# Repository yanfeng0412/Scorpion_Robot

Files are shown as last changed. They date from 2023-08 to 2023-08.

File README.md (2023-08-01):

# Scorpion_Robot
 The hexapod scorpion robot is designed with MG995 servos to control the joint angles, providing 3 degrees of freedom for each joint. The robot has two hands and a tail joint designed using biomimetic principles. It uses both MG995 and SG90 servos for driving. The PWM signals for the servos are expanded to 32 channels using PCA9685.
 
# The main tasks of the project are as follows:
  1. 3D Modeling of the robot (Solidworks2022)
  2. PCB Circuit Design(Altium Designer)
  3. Establishment of the mathematical model simulation system for the robot(ROS-Gazebo, Pybullet and Matlab)
  4. Forward and inverse kinematic calculation for the robot.
  5. Robot GUI/HMI Design (HTML and Android Studio)
  6. Robot's Gait Design (Arduino IDE)

This project primarily controls 25 servos, thus requiring two PCA9685 modules to expand the PWM signals for the servos. The communication between PCA9685 and the ESP main controller is established using I2C protocol. Additionally, the addresses of the two PCA9685 modules need to be set as 0x40 and 0x41 to distinguish the communication targets.

# Documentation
## 1. 3D Model Scorpion Robot MG995

  The file is modeled based on the MG995 servo motor. The hand joints of the robot are driven by bevel gears to achieve freedom along the z-axis. Meanwhile, the tail joint of the robot is designed using a biomimetic mechanical finger structure as a reference.
## 2. 3D Model Scorpion Robot SG90

   The file is primarily designed using the SG90 servo motor for the robot. However, due to the limited driving torque of the SG90 and issues with the quality of plastic servos, this design version faces challenges in achieving the set objectives. As a result, it is only included here for reference purposes.
## 3. Control Code
   Inside, it is mainly divided into the following sections:
   ### 3.1 Gait Control
   Programming the robot's gait using forward kinematics algorithms.The two files represent the user interfaces (UI) for the robot's control system. One is developed using Android Studio, and the other is an HTML version.
       3.1.1
       Android Studio Version (Android Studio)
       3.1.2
       HTML Version (Arduino IDE + HTML)
   ### 3.2 Inverse Kinematic    
   The file mainly adjusts the robot's posture using inverse kinematics. Based on this, the inverse kinematics can be integrated with sensors like MPU6050 to achieve closed-loop control of the robot's motion/pose.
## 4. ESPCAM
   By programming ESPCAM, this file is used for the vision system of the robot.
## 5. PCB_Robot
   The file is the PCB circuit design of the robot, created using Altium Designer 23 to layout the components on the module.

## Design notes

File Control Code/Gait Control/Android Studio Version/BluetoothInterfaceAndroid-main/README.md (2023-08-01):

# BluetoothInterfaceAndroid
An app that is built using Android Studio and Java. Can be used to interface your android smartphone to a bluetooth device like HC-05 and transmit and receive data. 
It has 5 built in buttons that are mapped to control the direction of the motor(vehiche) in our case. But the buttons can be mapped to any values of choice by just long 
pressing and setting the value of them.
The UI of the app looks like below.

My project-1

Feel free to use the code and modify the contents according to your requirement. Also if anyone wants to modify or optimize the code can send their requests.

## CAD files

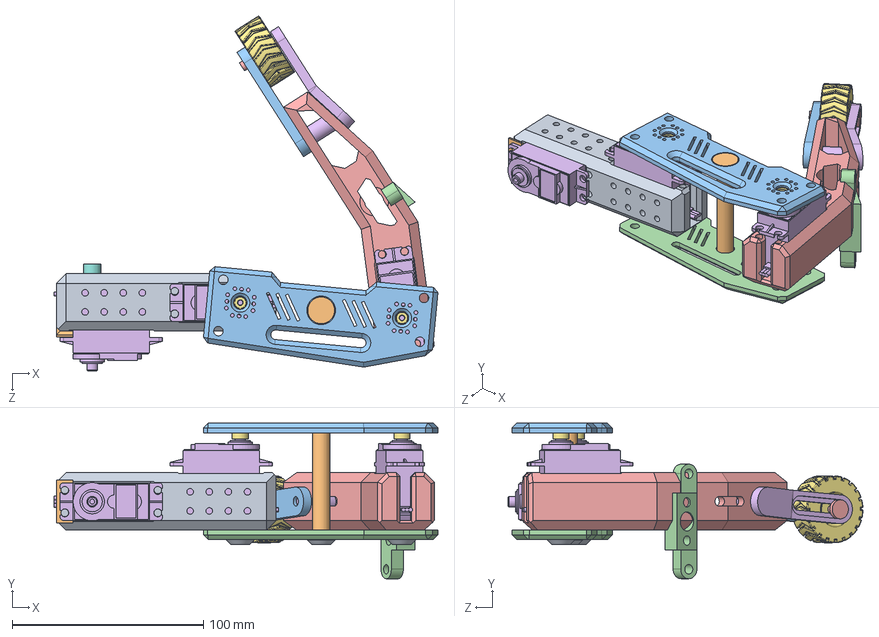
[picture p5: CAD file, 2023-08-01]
3D Model Scorpion Robot MG995/LEG3/LASM.SLDASM
201.0 x 81.4 x 185.8 mm
L0
L1
L2
L3
L4
MG995Servo x 3
wheel_MG995 x 2
L5 x 3
L6 x 3
L7
WheelLink2
L8
WheelLink4
WheelLink
wheel

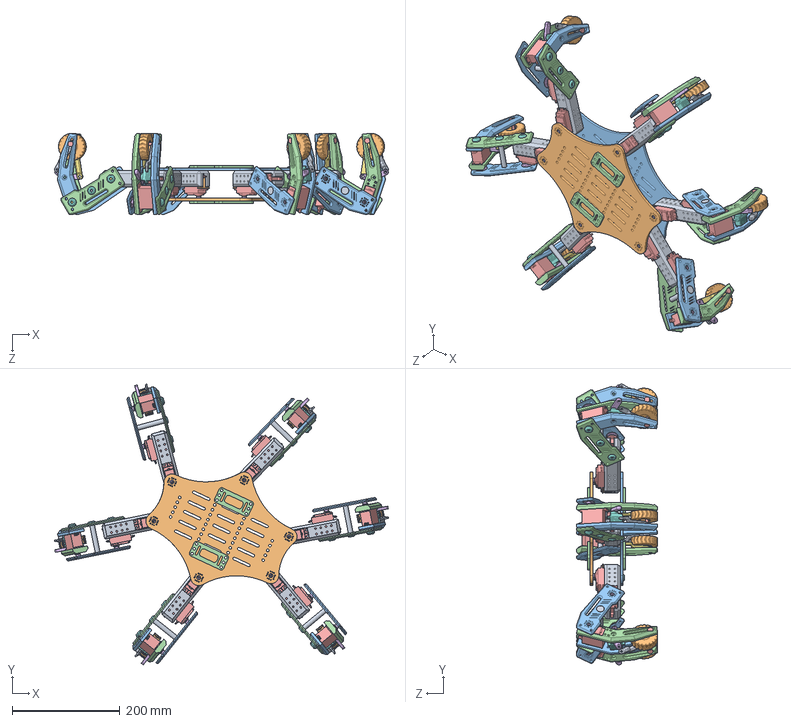
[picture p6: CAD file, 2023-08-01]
3D Model Scorpion Robot MG995/OVR2.SLDASM
621.1 x 522.3 x 151.2 mm
L0 x 6
L1 x 6
L2 x 6
L3 x 6
MG995Servo x 18
wheel_MG995 x 18
L5 x 19
L6 x 19
L7 x 6
wheel x 6
L4.1 x 6
L4.2 x 6
WheelLink4 x 12
WL2 x 6
WL1 x 6
SG90 - Micro Servo 9g - Tower Pro.1 x 6
WL3 x 6
base4.1
base3.1
cnl x 4

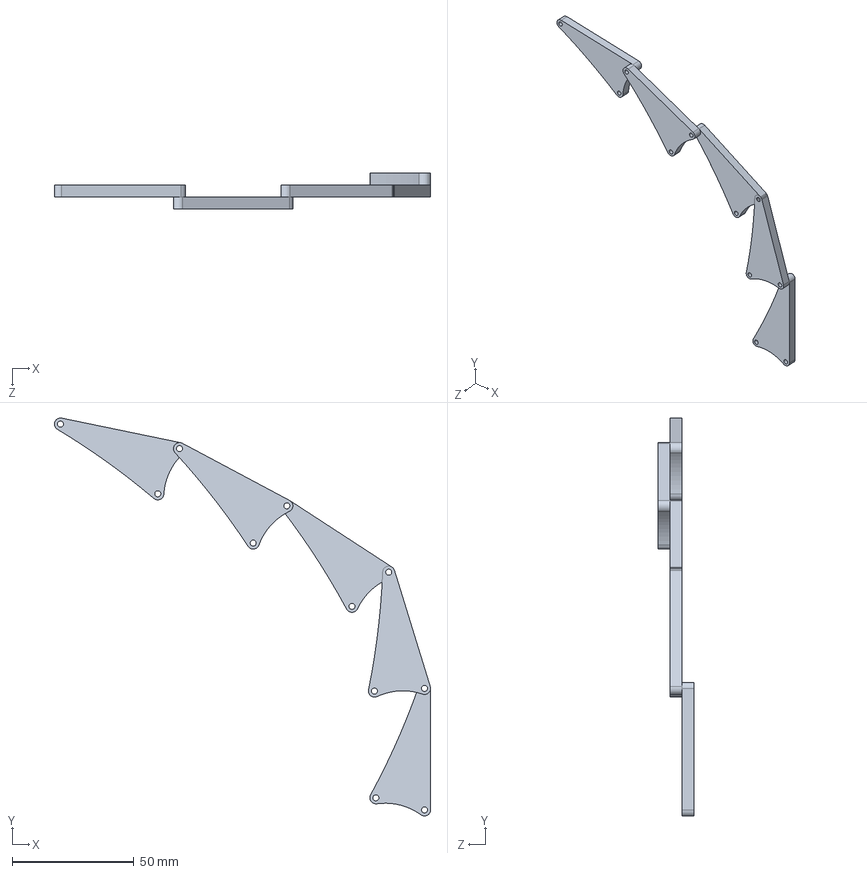
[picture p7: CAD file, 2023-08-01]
3D Model Scorpion Robot MG995/Tail/TailAssem.SLDASM
154.7 x 163.7 x 15.0 mm
T4 x 5

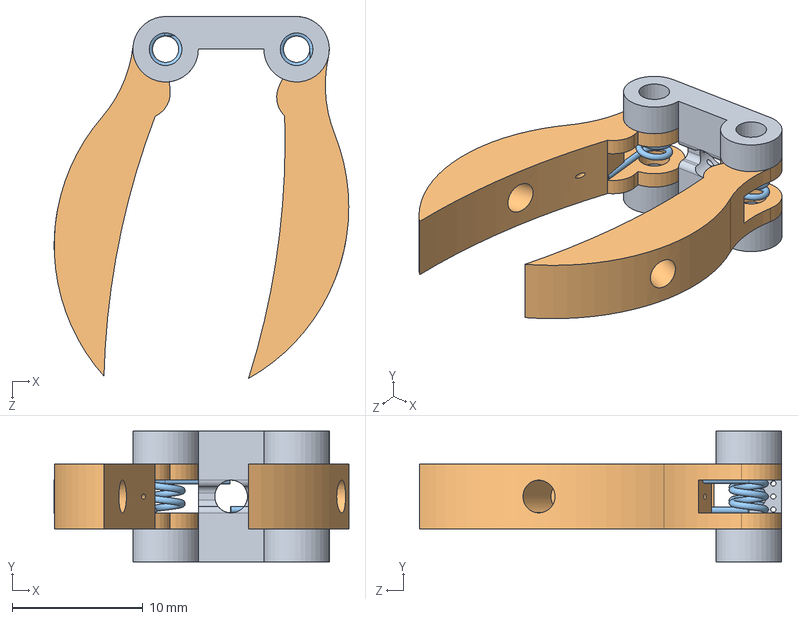
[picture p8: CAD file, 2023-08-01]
3D Model Scorpion Robot SG90/Hand/Claw2.SLDASM
22.5 x 10.0 x 27.6 mm
Claw1
Claw2 x 2
clawspring x 2

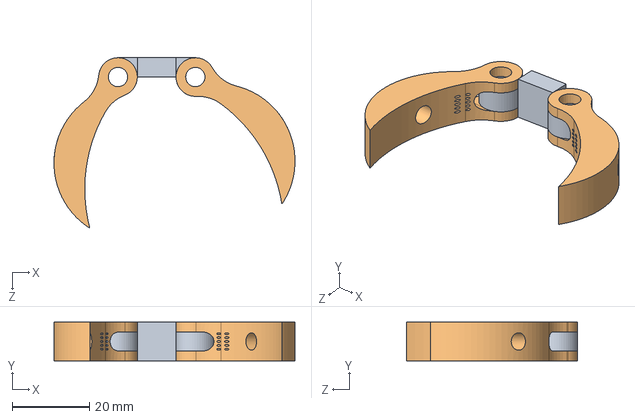
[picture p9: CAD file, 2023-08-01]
3D Model Scorpion Robot SG90/Hand2/ClawAse.SLDASM
62.3 x 10.0 x 44.1 mm
Claw1
Claw2 x 2

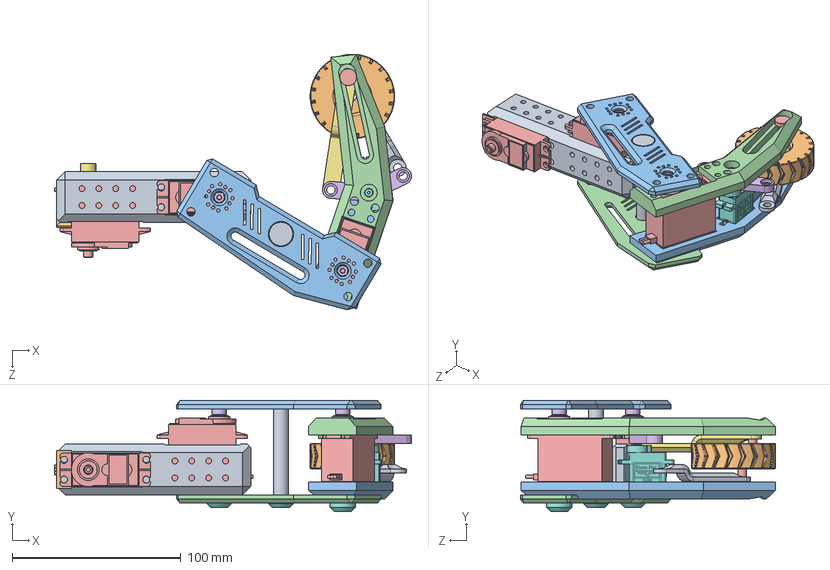
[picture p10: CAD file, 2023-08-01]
3D Model Scorpion Robot MG995/LEG2/LASM.SLDASM
211.3 x 65.9 x 151.2 mm
L0
L1
L2
L3
MG995Servo x 3
wheel_MG995 x 2
L5 x 3
L6 x 3
L7
wheel
L4.1
L4.2
WheelLink4 x 2
WL2
WL1
SG90 - Micro Servo 9g - Tower Pro.1
WL3

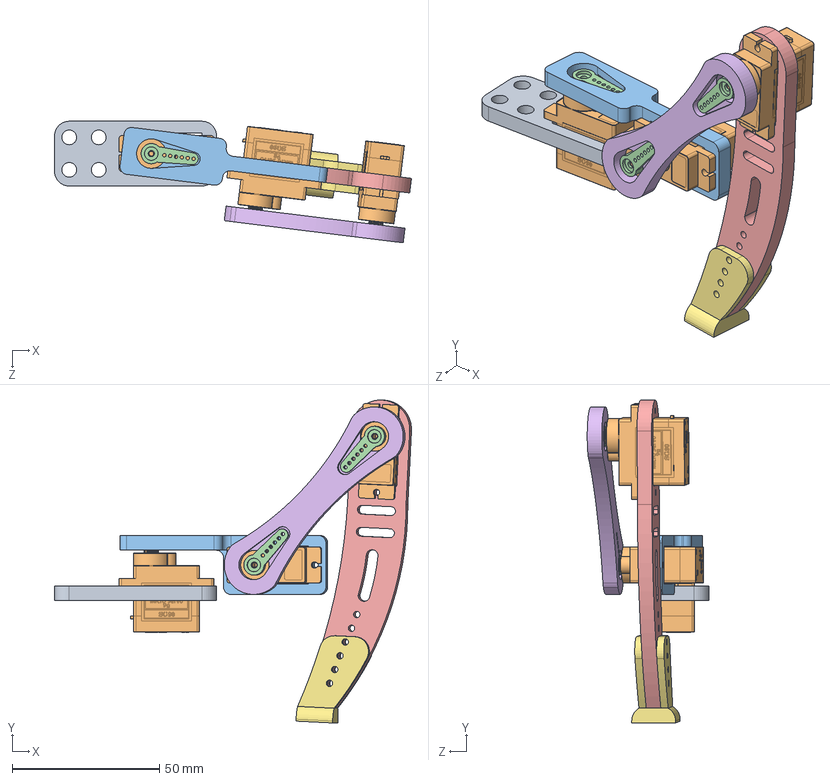
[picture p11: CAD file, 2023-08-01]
3D Model Scorpion Robot SG90/LegAs.SLDASM
121.1 x 109.6 x 41.3 mm
L1.0
SG90 - Micro Servo 9g - Tower Pro.1 x 3
L1
SG90 - Micro Servo 9g - Tower Pro.2 x 3
L3
L2
L4

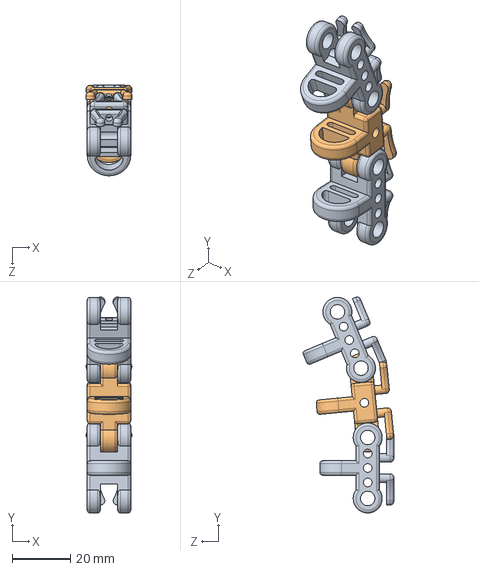
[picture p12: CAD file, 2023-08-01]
3D Model Scorpion Robot SG90/Tail/TAS/Assem1.SLDASM
15.8 x 74.4 x 31.2 mm
Tx1 x 2
Tx2

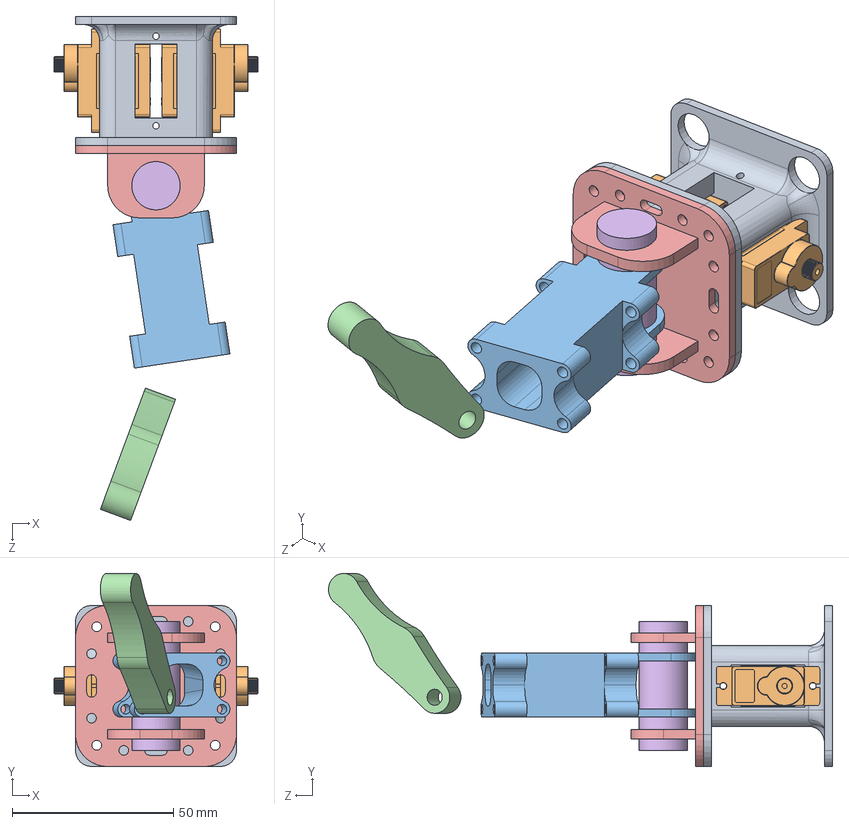
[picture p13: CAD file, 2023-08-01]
3D Model Scorpion Robot SG90/Tail/TAS2/As.SLDASM
63.3 x 59.9 x 156.4 mm
B1
SG90 - Micro Servo 9g - Tower Pro.1 x 2
T1
T2
T3
Strud

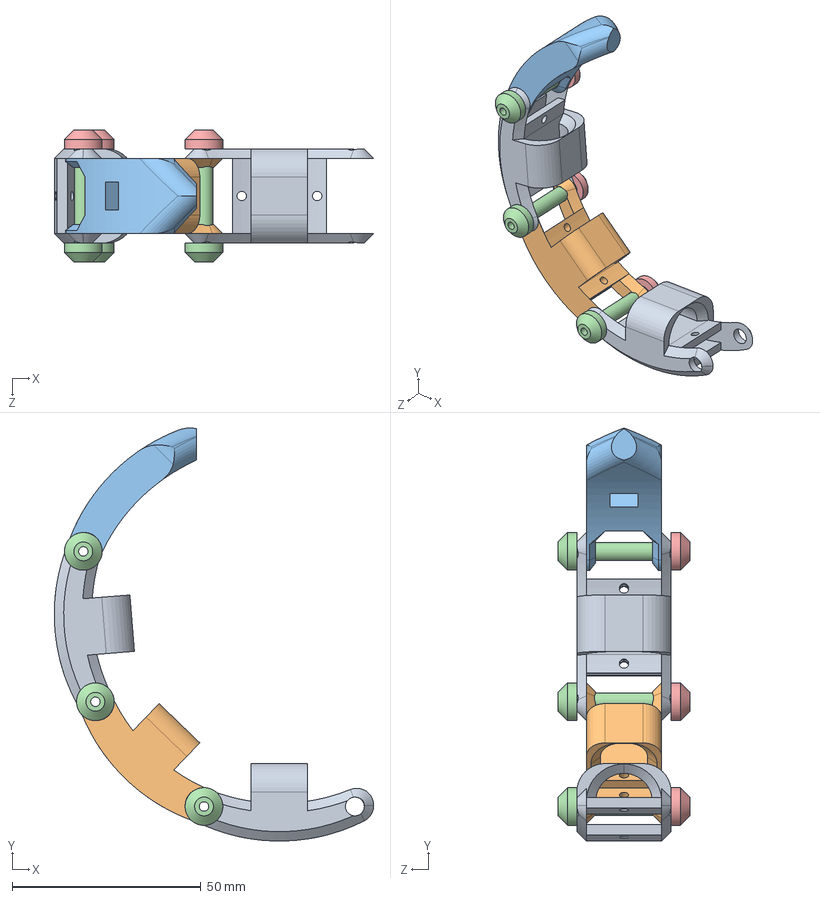
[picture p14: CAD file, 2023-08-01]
3D Model Scorpion Robot SG90/Tail/TailTensor/ase.SLDASM
84.7 x 109.5 x 35.0 mm
t2 x 2
t3
t4
nut x 3
bolt x 3

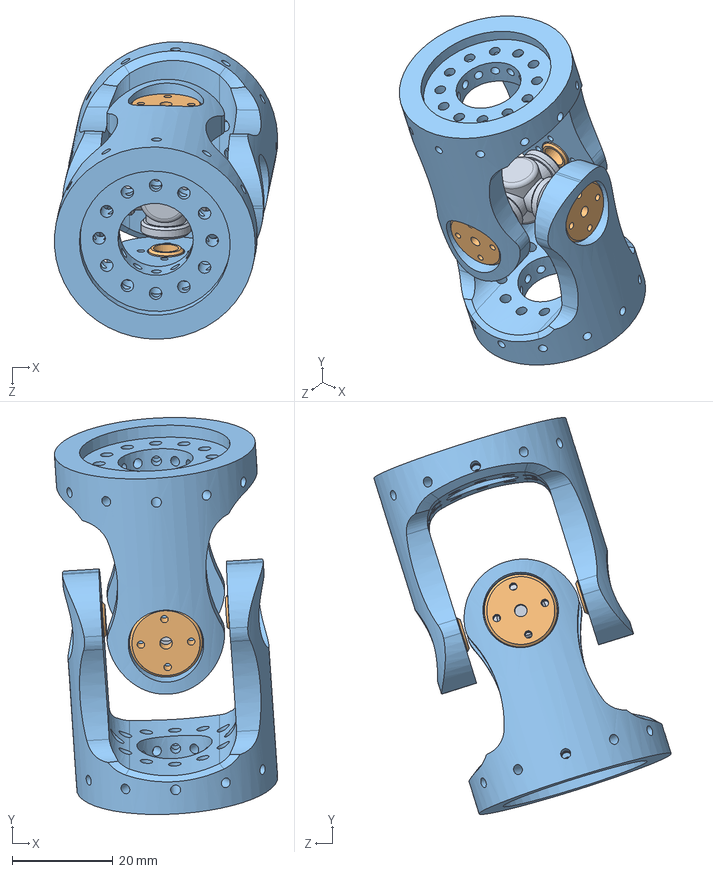
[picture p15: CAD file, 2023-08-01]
3D Model Scorpion Robot SG90/Tail/UVSTail2/Tail 2.SLDASM
44.4 x 78.9 x 59.1 mm
uvs2
uvs4 x 4
uvs1.2 x 2

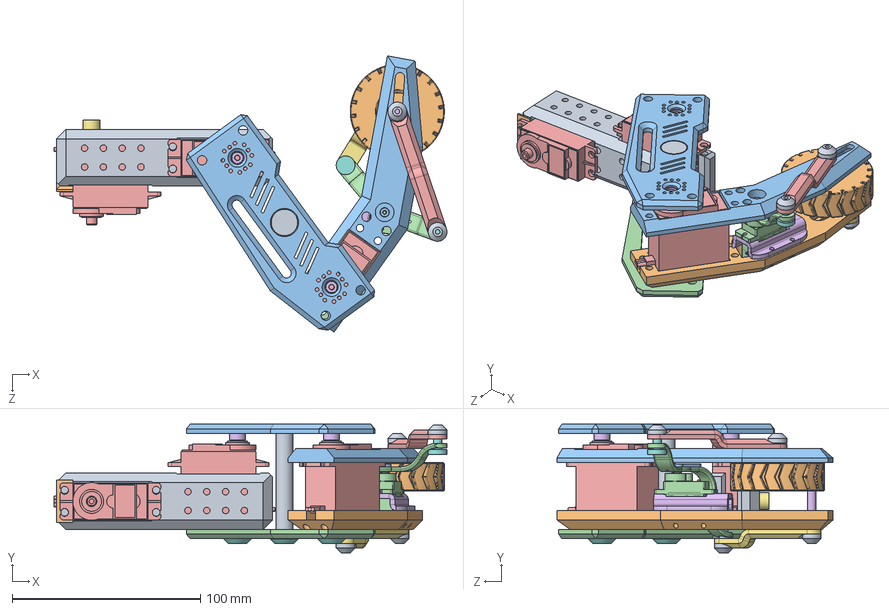
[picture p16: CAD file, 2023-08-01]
3D Model Scorpion Robot MG995/LEG4/LGASM2.SLDASM
209.0 x 68.4 x 146.9 mm
LG0
LG1
LG2
LG3
MG995Servo x 3
wheel_MG995 x 2
LG5 x 3
LG6 x 3
LG7
LG4.1
LG4.2
SG90 - Micro Servo 9g - Tower Pro.1
WL1
WL4 x 2
WL3
WL5 x 2
WLNUT1 x 4
wheel
SG90 - Micro Servo 9g - Tower Pro.2
WL2AS1
WL6
WL7

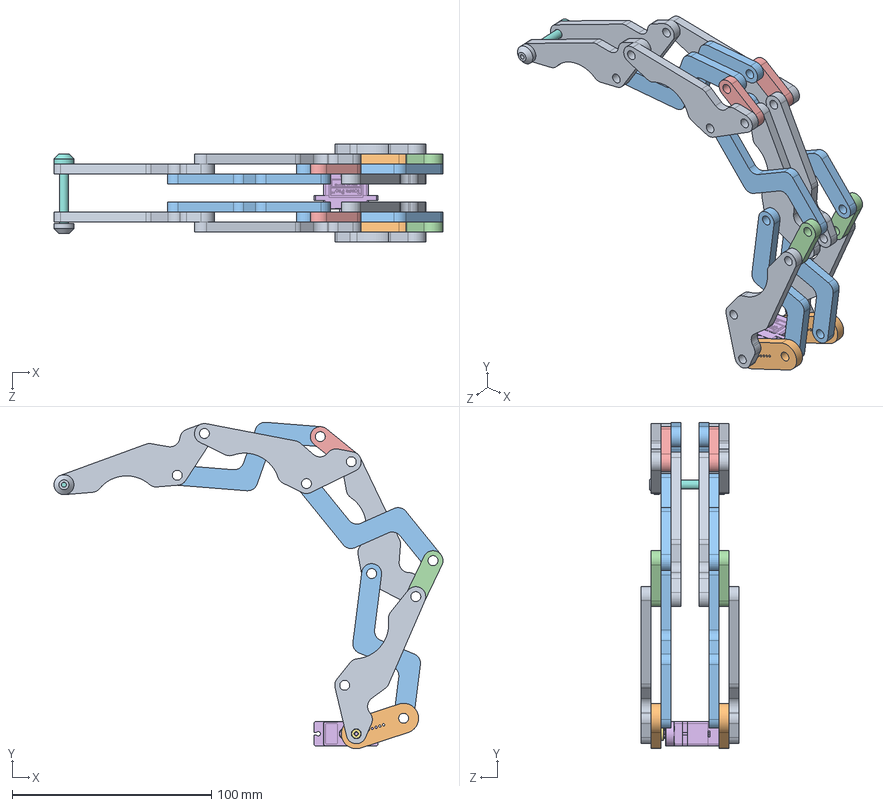
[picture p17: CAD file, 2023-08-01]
3D Model Scorpion Robot MG995/Tail3/Tail3Asm2.SLDASM
195.1 x 163.7 x 49.2 mm
T1 x 8
T2 x 2
T3 x 6
T4 x 2
T5 x 2
SG90 - Micro Servo 9g - Tower Pro.1
SG90 - Micro Servo 9g - Tower Pro.2
TL3
TL2

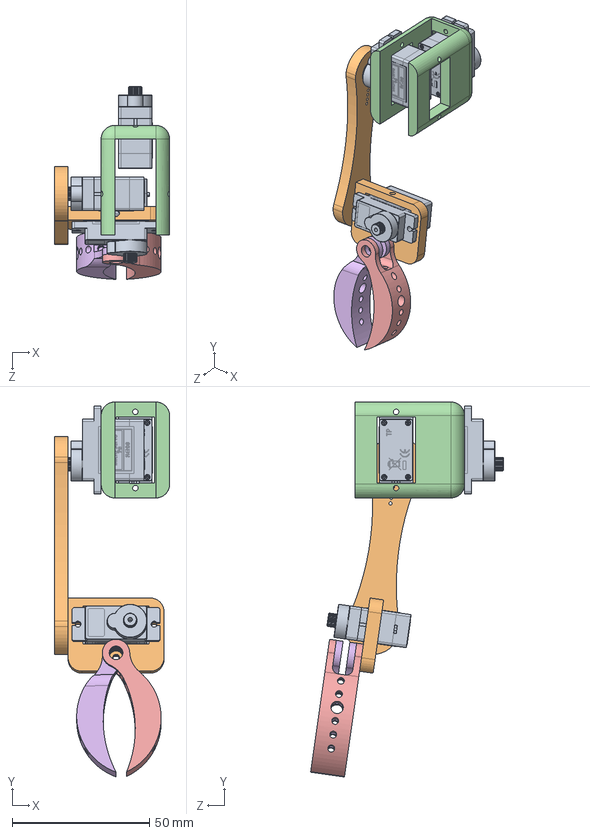
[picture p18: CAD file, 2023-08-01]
3D Model Scorpion Robot SG90/Hand/HandAsem.SLDASM
42.0 x 136.8 x 70.3 mm
SG90 - Micro Servo 9g - Tower Pro.1 x 3
hand6
SG90 - Micro Servo 9g - Tower Pro.2
hand5.1
Claw4
Claw4.1

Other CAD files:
3D Model Scorpion Robot SG90/Hand2/ClawAse2.SLDASM
3D Model Scorpion Robot MG995/Tail3/Tail3Asm.SLDASM
3D Model Scorpion Robot MG995/OVR3.SLDASM
3D Model Scorpion Robot MG995/Tail2/Tail2Asm.SLDASM
3D Model Scorpion Robot MG995/Hand1/Claw1.SLDPRT
3D Model Scorpion Robot MG995/Hand1/Claw2.SLDPRT
3D Model Scorpion Robot MG995/Hand1/Claw3.SLDPRT
3D Model Scorpion Robot MG995/Hand1/ClawAsm.SLDASM
3D Model Scorpion Robot MG995/Hand1/ClawLink1.SLDPRT
3D Model Scorpion Robot MG995/Hand1/ClawLink2.SLDPRT
3D Model Scorpion Robot MG995/Hand1/HL0.1.1.SLDPRT
3D Model Scorpion Robot MG995/Hand1/HL0.1.2.SLDPRT
3D Model Scorpion Robot MG995/Hand1/HL0.2.SLDPRT
3D Model Scorpion Robot MG995/Hand1/HL0.SLDPRT
3D Model Scorpion Robot MG995/Hand1/HL1.SLDPRT
3D Model Scorpion Robot MG995/Hand1/HL2.SLDPRT
3D Model Scorpion Robot MG995/Hand1/HandAsm.SLDASM
3D Model Scorpion Robot MG995/Hand1/HandBase1.SLDPRT
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

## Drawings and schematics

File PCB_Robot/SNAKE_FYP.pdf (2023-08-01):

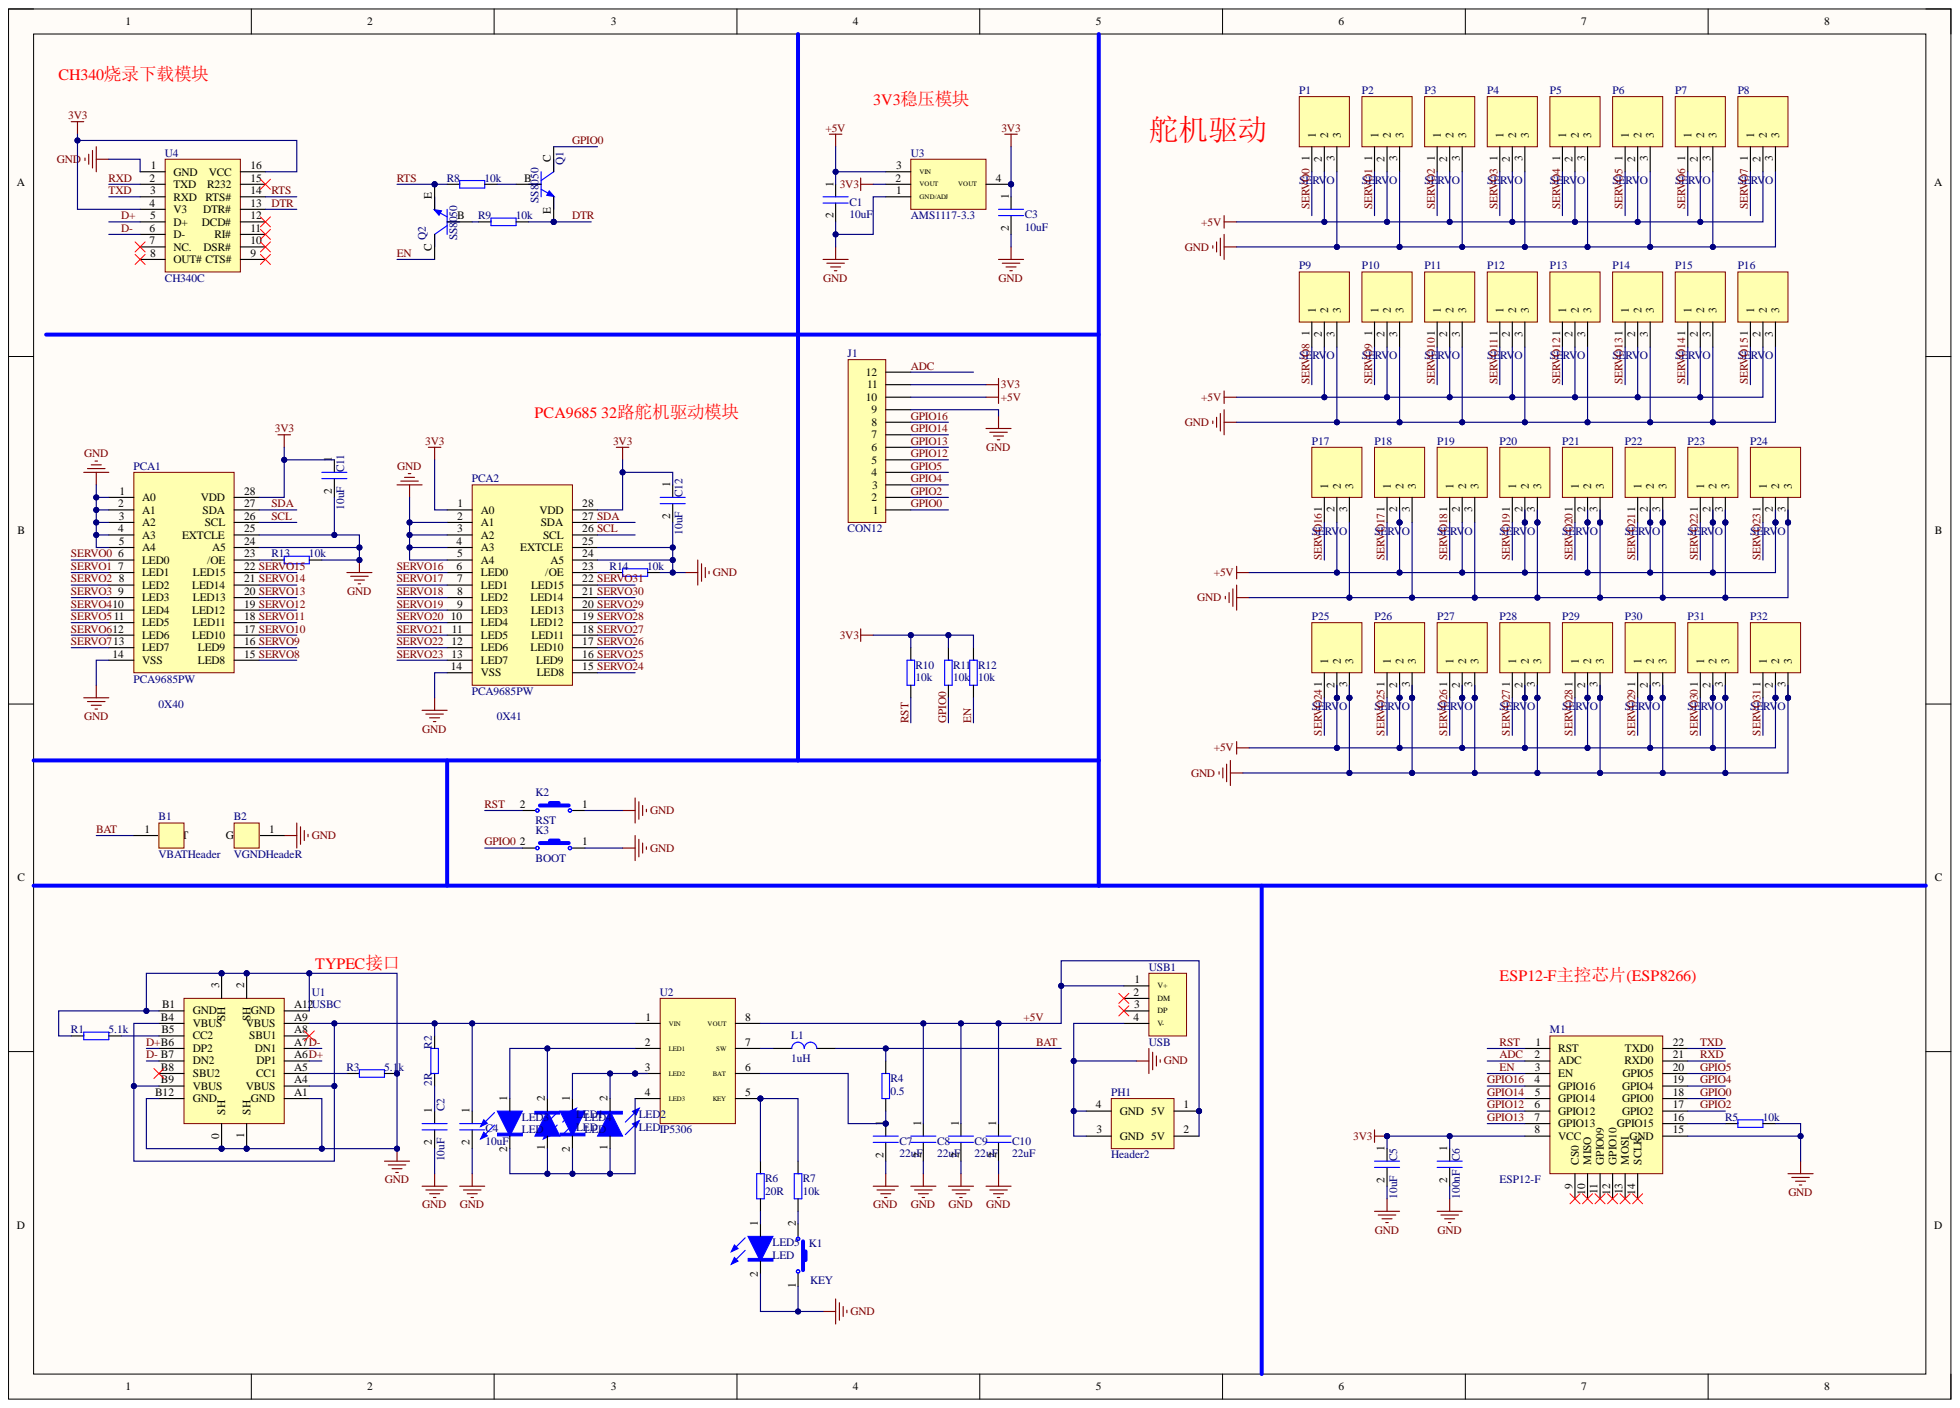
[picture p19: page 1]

SH 1 GND A1 VBUS A4 CC1 A5 DP1 A6 DN1 A7 SBU1 A8 VBUS A9 GND A12

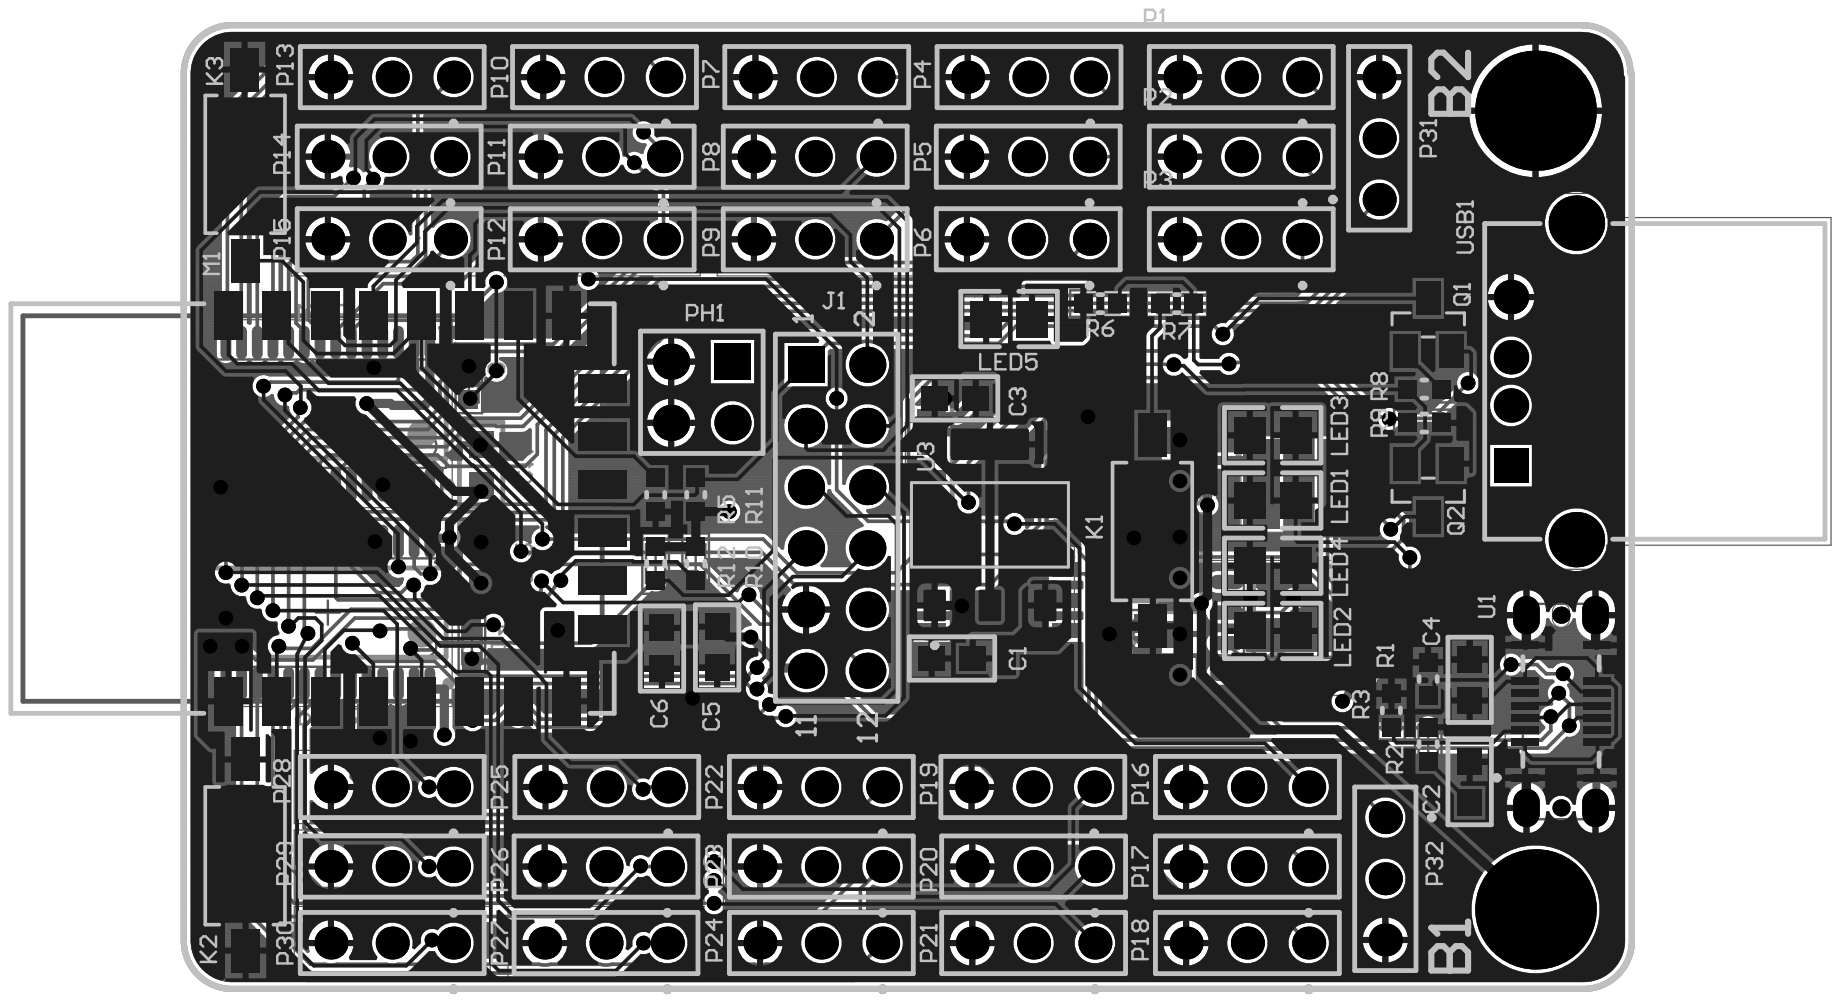
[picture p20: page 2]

Comment | Description | Designator | Footprint | LibRef | Quantity
VBATHeader | | B1 | 18650VBAT | VBATHeader | 1
VGNDHeadeR | | B2 | 18650GND | VGNDHeadeR | 1
10uF | 电容 | C1, C2, C3, C4, C5, C11, C12 | Cap-0603 | CAP | 7
100nF | 电容 | C6 | Cap-0603 | CAP | 1
22uF | 电容 | C7, C8, C9, C10 | Cap-0603 | CAP | 4
CON12 | Connector | J1 | HDR2X6 | CON12 | 1
KEY | 按键 | K1 | TSW SMD-3*6*2.5(Button) | RST | 1
RST | 按键 | K2 | TSW SMD-3*6*2.5(Button) | RST | 1
BOOT | 按键 | K3 | TSW SMD-3*6*2.5(Button) | RST | 1
1uH | 电感 | L1 | CDRH3D16_4.2*1.8 | INDUCTOR | 1
LED | | LED1, LED2, LED3, LED4, LED5 | LED-0805 | LED | 5
ESP12-F | | M1 | ESP-12F | ESP12-F | 1
SERVO | | P1, P2, P3, P4, P5, P6, P7, P8, P9, P10, P11, P12, P13, P14, P15, P16, P17, P18, P19, P20, P21, P22, P23, P24, P25, P26, P27, P28, P29, P30, P31, P32 | SERVOHEADER | SERVO | 32
PCA9685PW | | PCA1, PCA2 | PCA9685TSOP28 | PCA9685PW | 2
Header2 | | PH1 | HDR2X2 | Header2 | 1
SS8050 | | Q1, Q2 | SOT-23_BEC(SS8050) | SS8050 | 2
5.1k | 电阻 | R1, R3 | 0603_RES | RES | 2
2R | 电阻 | R2 | 0603_RES | RES | 1
0.5 | 电阻 | R4 | 0603_RES | RES | 1
10k | 电阻 | R5, R7, R8, R9, R10, R11, R12, R13, R14 | 0603_RES | RES | 9
20R | 电阻 | R6 | 0603_RES | RES | 1
USBC | | U1 | TYPEC | USBC | 1
IP5306 | 升压、降压和锂电池 充电管理芯片 | U2 | ESOP_IP5306 | IP5306 | 1
AMS1117-3.3 | | U3 | SOT229P700X180-4N(AMS1117-3.3) | AMS1117-3.3 | 1
CH340C | | U4 | SO016_CH340 | CH340 | 1
USB | | USB1 | TypeA | USB | 1

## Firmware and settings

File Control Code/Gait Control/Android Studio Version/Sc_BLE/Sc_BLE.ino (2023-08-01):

 #include <Wire.h>
#include <Adafruit_PWMServoDriver.h>
Adafruit_PWMServoDriver pwm = Adafruit_PWMServoDriver(0x40);
Adafruit_PWMServoDriver pwm1 = Adafruit_PWMServoDriver(0x41);
#define SERVOMIN 102
#define SERVOMAX 500
#include <ESP32Servo.h>
#include "BluetoothSerial.h"

BluetoothSerial serialBT;
char cmd;



double a0; double a1; double a2; double a3;
int leg1[] = {0,1,2};int leg2[] = {3,4,5}; int leg3[] = {6,7,8};
int leg4[] = {9,10,11}; int leg5[] = {12,13,14}; int leg6[] = {15,0,1};


double theta1;
double theta2;
double theta3; 
double theta4;
double theta5;
double theta6;

// 更改tf k
void setup() {
  pwm.begin();
  pwm.setPWMFreq(50);
  pwm.setOscillatorFrequency(27000000);
  pwm1.begin();
  pwm1.setPWMFreq(50);
  pwm1.setOscillatorFrequency(27000000);
  Serial.begin(115200);
  serialBT.begin("ESP32-BT");
  pinMode(2,OUTPUT);
}

void loop(){
  if (serialBT.available()){
    cmd = serialBT.read();
  }
  if(cmd == '1'){
        forward(); 
        digitalWrite(2,HIGH);
     }
  if(cmd == '2'){
        backward(); 
        digitalWrite(2,LOW);
    }
  if(cmd == '3'){
        turnright(); 
        digitalWrite(2,HIGH);
    }
  if(cmd == '4'){
        turnleft(); 
        digitalWrite(2,LOW);
     }  
  if(cmd == '5'){
        stand(); 
        digitalWrite(2,HIGH);
     } 
  delay(100);
}




int angle2pulse(int angle){
  int pulse ;
  if (angle <= 180){
    pulse = map(angle, 0, 180, SERVOMIN, SERVOMAX);
  }
  return pulse;
}

double cubicsp(double _thetai, double _thetaf,double _tf,double t){
      //a0 = 70;a1 = 0;a2 = 30 ;a3 = -10;
      //double thetai=45; double thetaf=135;
      double _theta0;
//      a0 = _thetai;
//      a1 = 0;
//      a2 = 3/(pow(_tf,2))*(_thetaf - _thetai);
//      a3 = -2/(pow(_tf,3))*(_thetaf - _thetai);
//      _theta0 = a0 + a1*(t) +a2*(pow(t,2)) +a3*(pow(t,3));
    
      return _thetaf; 
  }

void tryit(){
  pwm.setPWM(2,0,angle2pulse(60));   
  pwm.setPWM(8,0,angle2pulse(60)); 
  pwm.setPWM(14,0,angle2pulse(60)); 
  pwm.setPWM(5,0,angle2pulse(120));   
  pwm.setPWM(11,0,angle2pulse(120)); 
  pwm.setPWM(17,0,angle2pulse(120));
}
void stand(){

  pwm.setPWM(0,0,angle2pulse(90));
  pwm.setPWM(1,0,angle2pulse(75));
  pwm.setPWM(2,0,angle2pulse(0));

  pwm.setPWM(6,0,angle2pulse(90));
  pwm.setPWM(7,0,angle2pulse(75));
  pwm.setPWM(8,0,angle2pulse(0));

  pwm.setPWM(12,0,angle2pulse(90));
  pwm.setPWM(13,0,angle2pulse(75));
  pwm.setPWM(14,0,angle2pulse(0));

  pwm.setPWM(3,0,angle2pulse(90));
  pwm.setPWM(4,0,angle2pulse(75));
  pwm.setPWM(5,0,angle2pulse(0));

  pwm.setPWM(9,0,angle2pulse(90));
  pwm.setPWM(10,0,angle2pulse(75));
  pwm.setPWM(11,0,angle2pulse(0));

  pwm.setPWM(15,0,angle2pulse(90));
  pwm1.setPWM(0,0,angle2pulse(75));
  pwm1.setPWM(1,0,angle2pulse(0));

}

void backward() {
  pwm.setPWM(0,0,angle2pulse(90));   
  pwm.setPWM(6,0,angle2pulse(90)); 
  pwm.setPWM(12,0,angle2pulse(90)); 
  //小腿1,3,5
  pwm.setPWM(1,0,angle2pulse(90));   
  pwm.setPWM(7,0,angle2pulse(90)); 
  pwm.setPWM(13,0,angle2pulse(90)); 
  //大腿1,3,5
  pwm.setPWM(2,0,angle2pulse(0));   
  pwm.setPWM(8,0,angle2pulse(0)); 
  pwm.setPWM(14,0,angle2pulse(0)); 
  //末腿2,4,6
  pwm.setPWM(3,0,angle2pulse(90));   
  pwm.setPWM(9,0,angle2pulse(90)); 
  pwm.setPWM(15,0,angle2pulse(90)); 
  //小腿2,4,6
  pwm.setPWM(4,0,angle2pulse(90));   
  pwm.setPWM(10,0,angle2pulse(90)); 
  pwm1.setPWM(0,0,angle2pulse(90)); 
  //大腿2,4,6
  pwm.setPWM(5,0,angle2pulse(0));   
  pwm.setPWM(11,0,angle2pulse(0)); 
  pwm1.setPWM(1,0,angle2pulse(0)); 

  delay(1000);     
  double timestep = 0.01; //1
  double tf = 0.2;
  for (double t = 0; t <= tf; t +=timestep) { 
    theta1 = cubicsp(90,60,tf,t); //小腿1,3,5
    theta2 =cubicsp(90,45,tf,t);// 大腿1,3,5
    theta3 = cubicsp(90,120,tf,t); //小腿2,4,6
    theta4 =cubicsp(60,60,tf,t);// 大腿2,4,6
    //末腿1,3,5
    pwm.setPWM(0,0,angle2pulse(theta1));   
    pwm.setPWM(6,0,angle2pulse(theta1)); 
    pwm.setPWM(12,0,angle2pulse(theta3)); 
    //小腿1,3,5
    pwm.setPWM(1,0,angle2pulse(theta2));   
    pwm.setPWM(7,0,angle2pulse(theta2)); 
    pwm.setPWM(13,0,angle2pulse(theta2)); 
    //大腿1,3,5
    pwm.setPWM(2,0,angle2pulse(0));   
    pwm.setPWM(8,0,angle2pulse(0)); 
    pwm.setPWM(14,0,angle2pulse(0)); 
    //末腿2,4,6
    pwm.setPWM(3,0,angle2pulse(theta3));   
    pwm.setPWM(9,0,angle2pulse(theta1)); 
    pwm.setPWM(15,0,angle2pulse(theta1)); 
    //小腿2,4,6
    pwm.setPWM(4,0,angle2pulse(theta4));   
    pwm.setPWM(10,0,angle2pulse(theta4)); 
    pwm1.setPWM(0,0,angle2pulse(theta4)); 
    //大腿2,4,6
    pwm.setPWM(5,0,angle2pulse(0));   
    pwm.setPWM(11,0,angle2pulse(0)); 
    pwm1.setPWM(1,0,angle2pulse(0)); 

    delay(timestep*1000);                      // waits 15 ms for the servo to reach the position
  }
  for(int j=0;j<1;j++){
  timestep = 0.01; //2
  tf = 0.2;
  for (double t = 0; t <= tf; t +=timestep) { 
    theta1 = cubicsp(60,60,tf,t); //小腿1,3,5
    theta2 =cubicsp(45,90,tf,t);// 大腿1,3,5
    theta3 = cubicsp(120,120,tf,t); //小腿2,4,6
    theta4 =cubicsp(90,90,tf,t);// 大腿2,4,6
    //末腿1,3,5
    pwm.setPWM(0,0,angle2pulse(theta1));   
    pwm.setPWM(6,0,angle2pulse(theta1)); 
    pwm.setPWM(12,0,angle2pulse(theta3)); 
    //小腿1,3,5
    pwm.setPWM(1,0,angle2pulse(theta2));   
    pwm.setPWM(7,0,angle2pulse(theta2)); 
    pwm.setPWM(13,0,angle2pulse(theta2)); 
    //大腿1,3,5
    pwm.setPWM(2,0,angle2pulse(0));   
    pwm.setPWM(8,0,angle2pulse(0)); 
    pwm.setPWM(14,0,angle2pulse(0)); 
    //末腿2,4,6
    pwm.setPWM(3,0,angle2pulse(theta3));   
    pwm.setPWM(9,0,angle2pulse(theta1)); 
    pwm.setPWM(15,0,angle2pulse(theta1)); 
    //小腿2,4,6
    pwm.setPWM(4,0,angle2pulse(theta4));   
    pwm.setPWM(10,0,angle2pulse(theta4)); 
    pwm1.setPWM(0,0,angle2pulse(theta4)); 
    //大腿2,4,6
    pwm.setPWM(5,0,angle2pulse(0));   
    pwm.setPWM(11,0,angle2pulse(0)); 
    pwm1.setPWM(1,0,angle2pulse(0));  

    delay(timestep*1000);                      // waits 15 ms for the servo to reach the position
  }

  timestep = 0.01; //3
  tf = 0.4;
  for (double t = 0; t <= tf; t +=timestep) { 
    theta1 = cubicsp(60,120,tf,t); //小腿1,3,5
    theta2 =cubicsp(90,90,tf,t);// 大腿1,3,5
    theta3 = cubicsp(120,60,tf,t); //小腿2,4,6
    theta4 =cubicsp(90,45,tf,t);// 大腿2,4,6
    //末腿1,3,5
    pwm.setPWM(0,0,angle2pulse(theta1));   
    pwm.setPWM(6,0,angle2pulse(theta1)); 
    pwm.setPWM(12,0,angle2pulse(theta3)); 
    //小腿1,3,5
    pwm.setPWM(1,0,angle2pulse(theta2));   
    pwm.setPWM(7,0,angle2pulse(theta2)); 
    pwm.setPWM(13,0,angle2pulse(theta2)); 
    //大腿1,3,5
    pwm.setPWM(2,0,angle2pulse(0));   
    pwm.setPWM(8,0,angle2pulse(0)); 
    pwm.setPWM(14,0,angle2pulse(0)); 
    //末腿2,4,6
    pwm.setPWM(3,0,angle2pulse(theta3));   
    pwm.setPWM(9,0,angle2pulse(theta1)); 
    pwm.setPWM(15,0,angle2pulse(theta1)); 
    //小腿2,4,6
    pwm.setPWM(4,0,angle2pulse(theta4));   
    pwm.setPWM(10,0,angle2pulse(theta4)); 
    pwm1.setPWM(0,0,angle2pulse(theta4)); 
    //大腿2,4,6
    pwm.setPWM(5,0,angle2pulse(0));   
    pwm.setPWM(11,0,angle2pulse(0)); 
    pwm1.setPWM(1,0,angle2pulse(0));  

    delay(timestep*1000);                      // waits 15 ms for the servo to reach the position
  }

  timestep = 0.01; //4
  tf = 0.2;
  for (double t = 0; t <= tf; t +=timestep) { 
    theta1 = cubicsp(120,120,tf,t); //小腿1,3,5
    theta2 =cubicsp(90,90,tf,t);// 大腿1,3,5
    theta3 = cubicsp(60,60,tf,t); //小腿2,4,6
    theta4 =cubicsp(45,90,tf,t);// 大腿2,4,6
    //末腿1,3,5
    pwm.setPWM(0,0,angle2pulse(theta1));   
    pwm.setPWM(6,0,angle2pulse(theta1)); 
    pwm.setPWM(12,0,angle2pulse(theta3)); 
    //小腿1,3,5
    pwm.setPWM(1,0,angle2pulse(theta2));   
    pwm.setPWM(7,0,angle2pulse(theta2)); 
    pwm.setPWM(13,0,angle2pulse(theta2)); 
    //大腿1,3,5
    pwm.setPWM(2,0,angle2pulse(0));   
    pwm.setPWM(8,0,angle2pulse(0)); 
    pwm.setPWM(14,0,angle2pulse(0)); 
    //末腿2,4,6
    pwm.setPWM(3,0,angle2pulse(theta3));   
    pwm.setPWM(9,0,angle2pulse(theta1)); 
    pwm.setPWM(15,0,angle2pulse(theta1)); 
    //小腿2,4,6
    pwm.setPWM(4,0,angle2pulse(theta4));   
    pwm.setPWM(10,0,angle2pulse(theta4)); 
    pwm1.setPWM(0,0,angle2pulse(theta4)); 
    //大腿2,4,6
    pwm.setPWM(5,0,angle2pulse(0));   
    pwm.setPWM(11,0,angle2pulse(0)); 
    pwm1.setPWM(1,0,angle2pulse(0));  

    delay(timestep*1000);                      // waits 15 ms for the servo to reach the position
  }

  timestep = 0.01; //5
  tf = 0.4;
  for (double t = 0; t <= tf; t +=timestep) { 
    theta1 = cubicsp(120,60,tf,t); //小腿1,3,5
    theta2 =cubicsp(90,45,tf,t);// 大腿1,3,5
    theta3 = cubicsp(60,120,tf,t); //小腿2,4,6
    theta4 =cubicsp(90,90,tf,t);// 大腿2,4,6
    //末腿1,3,5
    pwm.setPWM(0,0,angle2pulse(theta1));   
    pwm.setPWM(6,0,angle2pulse(theta1)); 
    pwm.setPWM(12,0,angle2pulse(theta3)); 
    //小腿1,3,5
    pwm.setPWM(1,0,angle2pulse(theta2));   
    pwm.setPWM(7,0,angle2pulse(theta2)); 
    pwm.setPWM(13,0,angle2pulse(theta2)); 
    //大腿1,3,5
    pwm.setPWM(2,0,angle2pulse(0));   
    pwm.setPWM(8,0,angle2pulse(0)); 
    pwm.setPWM(14,0,angle2pulse(0)); 
    //末腿2,4,6
    pwm.setPWM(3,0,angle2pulse(theta3));   
    pwm.setPWM(9,0,angle2pulse(theta1)); 
    pwm.setPWM(15,0,angle2pulse(theta1)); 
    //小腿2,4,6
    pwm.setPWM(4,0,angle2pulse(theta4));   
    pwm.setPWM(10,0,angle2pulse(theta4)); 
    pwm1.setPWM(0,0,angle2pulse(theta4)); 
    //大腿2,4,6
    pwm.setPWM(5,0,angle2pulse(0));   
    pwm.setPWM(11,0,angle2pulse(0)); 
    pwm1.setPWM(1,0,angle2pulse(0));  

    delay(timestep*1000);                      // waits 15 ms for the servo to reach the position
  }
  }
  pwm.setPWM(0,0,angle2pulse(90));   
  pwm.setPWM(6,0,angle2pulse(90)); 
  pwm.setPWM(12,0,angle2pulse(90)); 
  //小腿1,3,5
  pwm.setPWM(1,0,angle2pulse(90));   
  pwm.setPWM(7,0,angle2pulse(90)); 
  pwm.setPWM(13,0,angle2pulse(90)); 
  //大腿1,3,5
  pwm.setPWM(2,0,angle2pulse(0));   
  pwm.setPWM(8,0,angle2pulse(0)); 
  pwm.setPWM(14,0,angle2pulse(0)); 
  //末腿2,4,6
  pwm.setPWM(3,0,angle2pulse(90));   
  pwm.setPWM(9,0,angle2pulse(90)); 
  pwm.setPWM(15,0,angle2pulse(90)); 
  //小腿2,4,6
  pwm.setPWM(4,0,angle2pulse(90));   
  pwm.setPWM(10,0,angle2pulse(90)); 
  pwm1.setPWM(0,0,angle2pulse(90)); 
  //大腿2,4,6
  pwm.setPWM(5,0,angle2pulse(0));   
  pwm.setPWM(11,0,angle2pulse(0)); 
  pwm1.setPWM(1,0,angle2pulse(0));
}

void forward() {
  pwm.setPWM(0,0,angle2pulse(90));   
  pwm.setPWM(6,0,angle2pulse(90)); 
  pwm.setPWM(12,0,angle2pulse(90)); 
  //小腿1,3,5
  pwm.setPWM(1,0,angle2pulse(90));   
  pwm.setPWM(7,0,angle2pulse(90)); 
  pwm.setPWM(13,0,angle2pulse(90)); 
  //大腿1,3,5
  pwm.setPWM(2,0,angle2pulse(0));   
  pwm.setPWM(8,0,angle2pulse(0)); 
  pwm.setPWM(14,0,angle2pulse(0)); 
  //末腿2,4,6
  pwm.setPWM(3,0,angle2pulse(90));   
  pwm.setPWM(9,0,angle2pulse(90)); 
  pwm.setPWM(15,0,angle2pulse(90)); 
  //小腿2,4,6
  pwm.setPWM(4,0,angle2pulse(90));   
  pwm.setPWM(10,0,angle2pulse(90)); 
  pwm1.setPWM(0,0,angle2pulse(90)); 
  //大腿2,4,6
  pwm.setPWM(5,0,angle2pulse(0));   
  pwm.setPWM(11,0,angle2pulse(0)); 
  pwm1.setPWM(1,0,angle2pulse(0)); 

  delay(1000);     
  double timestep = 0.01; //1
  double tf = 0.2;
  for (double t = 0; t <= tf; t +=timestep) { 
    theta1 = cubicsp(90,60,tf,t); //小腿1,3,5
    theta2 =cubicsp(90,90,tf,t);// 大腿1,3,5
    theta3 = cubicsp(90,120,tf,t); //小腿2,4,6
    theta4 =cubicsp(90,45,tf,t);// 大腿2,4,6
    //末腿1,3,5
    pwm.setPWM(0,0,angle2pulse(theta1));   
    pwm.setPWM(6,0,angle2pulse(theta1)); 
    pwm.setPWM(12,0,angle2pulse(theta3)); 
    //小腿1,3,5
    pwm.setPWM(1,0,angle2pulse(theta2));   
    pwm.setPWM(7,0,angle2pulse(theta2)); 
    pwm.setPWM(13,0,angle2pulse(theta2)); 
    //大腿1,3,5
    pwm.setPWM(2,0,angle2pulse(0));   
    pwm.setPWM(8,0,angle2pulse(0)); 
    pwm.setPWM(14,0,angle2pulse(0)); 
    //末腿2,4,6
    pwm.setPWM(3,0,angle2pulse(theta3));   
    pwm.setPWM(9,0,angle2pulse(theta1)); 
    pwm.setPWM(15,0,angle2pulse(theta1)); 
    //小腿2,4,6
    pwm.setPWM(4,0,angle2pulse(theta4));   
    pwm.setPWM(10,0,angle2pulse(theta4)); 
    pwm1.setPWM(0,0,angle2pulse(theta4)); 
    //大腿2,4,6
    pwm.setPWM(5,0,angle2pulse(0));   
    pwm.setPWM(11,0,angle2pulse(0)); 
    pwm1.setPWM(1,0,angle2pulse(0)); 

    delay(timestep*1000);                      // waits 15 ms for the servo to reach the position
  }
  for(int j=0;j<1;j++){
  timestep = 0.01; //2
  tf = 0.2;
  for (double t = 0; t <= tf; t +=timestep) { 
    theta1 = cubicsp(60,60,tf,t); //小腿1,3,5
    theta2 =cubicsp(90,90,tf,t);// 大腿1,3,5
    theta3 = cubicsp(120,120,tf,t); //小腿2,4,6
    theta4 =cubicsp(45,90,tf,t);// 大腿2,4,6
    //末腿1,3,5
    pwm.setPWM(0,0,angle2pulse(theta1));   
    pwm.setPWM(6,0,angle2pulse(theta1)); 
    pwm.setPWM(12,0,angle2pulse(theta3)); 
    //小腿1,3,5
    pwm.setPWM(1,0,angle2pulse(theta2));   
    pwm.setPWM(7,0,angle2pulse(theta2)); 
    pwm.setPWM(13,0,angle2pulse(theta2)); 
    //大腿1,3,5
    pwm.setPWM(2,0,angle2pulse(0));   
    pwm.setPWM(8,0,angle2pulse(0)); 
    pwm.setPWM(14,0,angle2pulse(0)); 
    //末腿2,4,6
    pwm.setPWM(3,0,angle2pulse(theta3));   
    pwm.setPWM(9,0,angle2pulse(theta1)); 
    pwm.setPWM(15,0,angle2pulse(theta1)); 
    //小腿2,4,6
    pwm.setPWM(4,0,angle2pulse(theta4));   
    pwm.setPWM(10,0,angle2pulse(theta4)); 
    pwm1.setPWM(0,0,angle2pulse(theta4)); 
    //大腿2,4,6
    pwm.setPWM(5,0,angle2pulse(0));   
    pwm.setPWM(11,0,angle2pulse(0)); 
    pwm1.setPWM(1,0,angle2pulse(0));  

    delay(timestep*1000);                      // waits 15 ms for the servo to reach the position
  }

  timestep = 0.01; //3
  tf = 0.4;
  for (double t = 0; t <= tf; t +=timestep) { 
    theta1 = cubicsp(60,120,tf,t); //小腿1,3,5
    theta2 =cubicsp(90,45,tf,t);// 大腿1,3,5
    theta3 = cubicsp(120,60,tf,t); //小腿2,4,6
    theta4 =cubicsp(90,90,tf,t);// 大腿2,4,6
    //末腿1,3,5
    pwm.setPWM(0,0,angle2pulse(theta1));   
    pwm.setPWM(6,0,angle2pulse(theta1)); 
    pwm.setPWM(12,0,angle2pulse(theta3)); 
    //小腿1,3,5
    pwm.setPWM(1,0,angle2pulse(theta2));   
    pwm.setPWM(7,0,angle2pulse(theta2)); 
    pwm.setPWM(13,0,angle2pulse(theta2)); 
    //大腿1,3,5
    pwm.setPWM(2,0,angle2pulse(0));   
    pwm.setPWM(8,0,angle2pulse(0)); 
    pwm.setPWM(14,0,angle2pulse(0)); 
    //末腿2,4,6
    pwm.setPWM(3,0,angle2pulse(theta3));   
    pwm.setPWM(9,0,angle2pulse(theta1)); 
    pwm.setPWM(15,0,angle2pulse(theta1)); 
    //小腿2,4,6
    pwm.setPWM(4,0,angle2pulse(theta4));   
    pwm.setPWM(10,0,angle2pulse(theta4)); 
    pwm1.setPWM(0,0,angle2pulse(theta4)); 
    //大腿2,4,6
    pwm.setPWM(5,0,angle2pulse(0));   
    pwm.setPWM(11,0,angle2pulse(0)); 
    pwm1.setPWM(1,0,angle2pulse(0));  

    delay(timestep*1000);                      // waits 15 ms for the servo to reach the position
  }

  timestep = 0.01; //4
  tf = 0.2;
  for (double t = 0; t <= tf; t +=timestep) { 
    theta1 = cubicsp(120,120,tf,t); //小腿1,3,5
    theta2 =cubicsp(45,90,tf,t);// 大腿1,3,5
    theta3 = cubicsp(60,60,tf,t); //小腿2,4,6
    theta4 =cubicsp(90,90,tf,t);// 大腿2,4,6
    //末腿1,3,5
    pwm.setPWM(0,0,angle2pulse(theta1));   
    pwm.setPWM(6,0,angle2pulse(theta1)); 
    pwm.setPWM(12,0,angle2pulse(theta3)); 
    //小腿1,3,5
    pwm.setPWM(1,0,angle2pulse(theta2));   
    pwm.setPWM(7,0,angle2pulse(theta2)); 
    pwm.setPWM(13,0,angle2pulse(theta2)); 
    //大腿1,3,5
    pwm.setPWM(2,0,angle2pulse(0));   
    pwm.setPWM(8,0,angle2pulse(0)); 
    pwm.setPWM(14,0,angle2pulse(0)); 
    //末腿2,4,6
    pwm.setPWM(3,0,angle2pulse(theta3));   
    pwm.setPWM(9,0,angle2pulse(theta1)); 
    pwm.setPWM(15,0,angle2pulse(theta1)); 
    //小腿2,4,6
    pwm.setPWM(4,0,angle2pulse(theta4));   
    pwm.setPWM(10,0,angle2pulse(theta4)); 
    pwm1.setPWM(0,0,angle2pulse(theta4)); 
    //大腿2,4,6
    pwm.setPWM(5,0,angle2pulse(0));   
    pwm.setPWM(11,0,angle2pulse(0)); 
    pwm1.setPWM(1,0,angle2pulse(0));  

    delay(timestep*1000);                      // waits 15 ms for the servo to reach the position
  }

  timestep = 0.01; //5
  tf = 0.4;
  for (double t = 0; t <= tf; t +=timestep) { 
    theta1 = cubicsp(120,60,tf,t); //小腿1,3,5
    theta2 =cubicsp(90,90,tf,t);// 大腿1,3,5
    theta3 = cubicsp(60,120,tf,t); //小腿2,4,6
    theta4 =cubicsp(90,45,tf,t);// 大腿2,4,6
    //末腿1,3,5
    pwm.setPWM(0,0,angle2pulse(theta1));   
    pwm.setPWM(6,0,angle2pulse(theta1)); 
    pwm.setPWM(12,0,angle2pulse(theta3)); 
    //小腿1,3,5
    pwm.setPWM(1,0,angle2pulse(theta2));   
    pwm.setPWM(7,0,angle2pulse(theta2)); 
    pwm.setPWM(13,0,angle2pulse(theta2)); 
    //大腿1,3,5
    pwm.setPWM(2,0,angle2pulse(0));   
    pwm.setPWM(8,0,angle2pulse(0)); 
    pwm.setPWM(14,0,angle2pulse(0)); 
    //末腿2,4,6
    pwm.setPWM(3,0,angle2pulse(theta3));   
    pwm.setPWM(9,0,angle2pulse(theta1)); 
    pwm.setPWM(15,0,angle2pulse(theta1)); 
    //小腿2,4,6
    pwm.setPWM(4,0,angle2pulse(theta4));   
    pwm.setPWM(10,0,angle2pulse(theta4)); 
    pwm1.setPWM(0,0,angle2pulse(theta4)); 
    //大腿2,4,6
    pwm.setPWM(5,0,angle2pulse(0));   
    pwm.setPWM(11,0,angle2pulse(0)); 
    pwm1.setPWM(1,0,angle2pulse(0));  

    delay(timestep*1000);                      // waits 15 ms for the servo to reach the position
  }
  }
  pwm.setPWM(0,0,angle2pulse(90));   
  pwm.setPWM(6,0,angle2pulse(90)); 
  pwm.setPWM(12,0,angle2pulse(90)); 
  //小腿1,3,5
  pwm.setPWM(1,0,angle2pulse(90));   
  pwm.setPWM(7,0,angle2pulse(90)); 
  pwm.setPWM(13,0,angle2pulse(90)); 
  //大腿1,3,5
  pwm.setPWM(2,0,angle2pulse(0));   
  pwm.setPWM(8,0,angle2pulse(0)); 
  pwm.setPWM(14,0,angle2pulse(0)); 
  //末腿2,4,6
  pwm.setPWM(3,0,angle2pulse(90));   
  pwm.setPWM(9,0,angle2pulse(90)); 
  pwm.setPWM(15,0,angle2pulse(90)); 
  //小腿2,4,6
  pwm.setPWM(4,0,angle2pulse(90));   
  pwm.setPWM(10,0,angle2pulse(90)); 
  pwm1.setPWM(0,0,angle2pulse(90)); 
  //大腿2,4,6
  pwm.setPWM(5,0,angle2pulse(0));   
  pwm.setPWM(11,0,angle2pulse(0)); 
  pwm1.setPWM(1,0,angle2pulse(0));
}

void initial(){
  pwm.setPWM(0,0,angle2pulse(90));
  pwm.setPWM(1,0,angle2pulse(135));
  pwm.setPWM(2,0,angle2pulse(0));

  pwm.setPWM(6,0,angle2pulse(90));
  pwm.setPWM(7,0,angle2pulse(135));
  pwm.setPWM(8,0,angle2pulse(0));

  pwm.setPWM(12,0,angle2pulse(90));
  pwm.setPWM(13,0,angle2pulse(135));
  pwm.setPWM(14,0,angle2pulse(0));

  pwm.setPWM(3,0,angle2pulse(90));
  pwm.setPWM(4,0,angle2pulse(135));
  pwm.setPWM(5,0,angle2pulse(0));

  pwm.setPWM(9,0,angle2pulse(90));
  pwm.setPWM(10,0,angle2pulse(135));
  pwm.setPWM(11,0,angle2pulse(0));

  pwm.setPWM(15,0,angle2pulse(90));
  pwm1.setPWM(0,0,angle2pulse(135));
  pwm1.setPWM(1,0,angle2pulse(0));

}
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

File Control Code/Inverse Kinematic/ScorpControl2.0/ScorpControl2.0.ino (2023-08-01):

#include <Wire.h>
#include <Adafruit_PWMServoDriver.h>

Adafruit_PWMServoDriver pwm = Adafruit_PWMServoDriver(0x40);
Adafruit_PWMServoDriver pwm1 = Adafruit_PWMServoDriver(0x41);
#define SERVOMIN 102
#define SERVOMAX 500
#include <ESP32Servo.h>

Servo myservo;  

float a0; float a1; float a2; float a3;


float currentFrontFemurR, currentFrontTibiaR, currentFrontCoxaR, currentMiddleFemurR, currentMiddleTibiaR, currentMiddleCoxaR, currentRearFemurR, currentRearTibiaR, currentRearCoxaR;
float currentFrontFemurL, currentFrontTibiaL, currentFrontCoxaL, currentMiddleFemurL, currentMiddleTibiaL, currentMiddleCoxaL, currentRearFemurL, currentRearTibiaL, currentRearCoxaL;



//robot dimensions 
float BodySideLength = 10.5;
float bodylength = 200; 

// Leg dimensions (modify these based on your robot's design)
const float COXA_LENGTH =77 ;   // length of coxa segment (mm)
const float FEMUR_LENGTH = 85;  // length of femur segment (mm)
const float TIBIA_LENGTH = 110;  // length of tibia segment (mm)

 
 


void moveUpDownTilt(float Z, float L1, float tiltX, float tiltY) {
    // Inverse Kinematics
    float coxaFL, femurFL, tibiaFL;
    float coxaFR, femurFR, tibiaFR;
    float coxaML, femurML, tibiaML;
    float coxaMR, femurMR, tibiaMR;
    float coxaBL, femurBL, tibiaBL;
    float coxaBR, femurBR, tibiaBR;

    // Front-left leg
    InverseKinematics(&coxaFL, &femurFL, &tibiaFL, Z-tiltY-tiltX, L1);
    // Front-right leg
    InverseKinematics(&coxaFR, &femurFR, &tibiaFR, Z-tiltY+tiltX, L1);
    // Middle-left leg
    InverseKinematics(&coxaML, &femurML, &tibiaML, Z-tiltX, L1);
    // Middle-right leg
    InverseKinematics(&coxaMR, &femurMR, &tibiaMR, Z+tiltX, L1);
    // Back-left leg
    InverseKinematics(&coxaBL, &femurBL, &tibiaBL, Z+tiltY-tiltX, L1);
    // Back-right leg
    InverseKinematics(&coxaBR, &femurBR, &tibiaBR, Z+tiltY+tiltX, L1);

    servoControl(femurFR, tibiaFR, coxaFR, femurMR, tibiaMR, coxaMR, femurBR, tibiaBR, coxaBR, 
                 femurFL, tibiaFL, coxaFL, femurML, tibiaML, coxaML, femurBL, tibiaBL, coxaBL);
    delay(500);

}





void twist(float twist) {

    // Inverse Kinematics
    float coxa,femur, tibia;
    
    InverseKinematics(&coxa, &femur, &tibia, 10, 45);
    
    float coxaT=coxa-twist;

    // Servo Control
    servoControl(femur, tibia, coxaT, femur, tibia, coxaT, femur, tibia, coxaT, femur, tibia, coxaT, femur, tibia, coxaT, femur, tibia, coxaT);
    delay(500);


}


void demo (){

  float coxa,femur, tibia;

  

float Z=20;
float L1=40;

  float tiltX = 0;
  float tiltY = 0;

 moveUpDownTilt(Z, L1, tiltX, tiltY);

  Z=40;

  moveUpDownTilt(Z, L1, tiltX, tiltY);
  
  Z=10;

  moveUpDownTilt(Z, L1, tiltX, tiltY);
  

float twistangle = 25;

twist(twistangle) ;

twistangle= -25;
twist(twistangle);


  Z=20;
  tiltX = 20;
  tiltY = 20;

 moveUpDownTilt(Z, L1, tiltX, tiltY);
            

   tiltX = -20;
   tiltY = -20;

 moveUpDownTilt(Z, L1, tiltX, tiltY);


   tiltX = 20;
   tiltY = -10;
 moveUpDownTilt(Z, L1, tiltX, tiltY);


 tiltX = -20;
   tiltY = 10;

    moveUpDownTilt(Z, L1, tiltX, tiltY);

  
}


float cubicsp(float _thetai, float _thetaf, double _tf, double t) {
  float _theta0;
  a0 = _thetai;
  a1 = 0;
  a2 = 3/(pow(_tf,2))*(_thetaf - _thetai);
  a3 = -2/(pow(_tf,3))*(_thetaf - _thetai);
  _theta0 = a0 + a1*(t) + a2*(pow(t,2)) + a3*(pow(t,3));
  return _theta0;
 
}






int angle2pulse(int angle){
  int pulse ;

  if (angle <= 180){
    pulse = map(angle, 0, 180, SERVOMIN, SERVOMAX);
  }
  return pulse;
}



void move(float distance, float speed) {
  
    float stepSize = 20;
    int steps = distance / stepSize;
    float timePerStep = 2000 / speed;

    // Starting from rest position
    float coxa[6] = {90, 90, 90, 90, 90, 90};
    float femur[6] = {70, 70, 70, 70, 70, 70};
    float tibia[6] = {0, 0, 0, 0, 0, 0};

    float deltaCoxa = stepSize;


   servoControl(femur[0], tibia[0], coxa[0], femur[1], tibia[1], coxa[1], femur[2], tibia[2], coxa[2],
                     femur[3], tibia[3], coxa[3], femur[4], tibia[4], coxa[4], femur[5], tibia[5], coxa[5]);


    for (int step = 0; step < steps; step++) {
      

        //move tripod 1 forward
        InverseKinematics(&coxa[0], &femur[0], &tibia[0], -10, 40);
        InverseKinematics(&coxa[2], &femur[2], &tibia[2], -10, 40);
        InverseKinematics(&coxa[4], &femur[4], &tibia[4], -10, 40);

        
        coxa[0] += deltaCoxa;
        coxa[2] += deltaCoxa;
        coxa[4] -= deltaCoxa;

        //move tripod 2 backward
        InverseKinematics(&coxa[1], &femur[1], &tibia[1], 0, 30);
        InverseKinematics(&coxa[3], &femur[3], &tibia[3],30, 30);
        InverseKinematics(&coxa[5], &femur[5], &tibia[5], 10, 30);
        coxa[1] -= deltaCoxa;
        coxa[3] += deltaCoxa;
        coxa[5] += deltaCoxa;



        delay(timePerStep / 2);
        servoControl(femur[0], tibia[0], coxa[0], femur[1], tibia[1], coxa[1], femur[2], tibia[2], coxa[2],
                     femur[3], tibia[3], coxa[3], femur[4], tibia[4], coxa[4], femur[5], tibia[5], coxa[5]);

        //move them all down
        InverseKinematics(&coxa[0], &femur[0], &tibia[0], 30, 40);
        InverseKinematics(&coxa[2], &femur[2], &tibia[2], 10, 40);
        InverseKinematics(&coxa[4], &femur[4], &tibia[4], 20, 40);

        InverseKinematics(&coxa[1], &femur[1], &tibia[1], 20, 30);
        InverseKinematics(&coxa[3], &femur[3], &tibia[3], 10, 30);
        InverseKinematics(&coxa[5], &femur[5], &tibia[5], 30, 30);

        delay(timePerStep / 4);
        servoControl(femur[0], tibia[0], coxa[0], femur[1], tibia[1], coxa[1], femur[2], tibia[2], coxa[2],
                     femur[3], tibia[3], coxa[3], femur[4], tibia[4], coxa[4], femur[5], tibia[5], coxa[5]);

        //Move tripod 1 backward
        InverseKinematics(&coxa[0], &femur[0], &tibia[0], 20, 30);
        InverseKinematics(&coxa[2], &femur[2], &tibia[2], 10, 30);
        InverseKinematics(&coxa[4], &femur[4], &tibia[4], 20, 30);
        coxa[0] -= deltaCoxa;
        coxa[2] -= deltaCoxa;
        coxa[4] += deltaCoxa;

        //move tripod 2 forward
        InverseKinematics(&coxa[1], &femur[1], &tibia[1], -10, 40);
        InverseKinematics(&coxa[3], &femur[3], &tibia[3], -10, 40);
        InverseKinematics(&coxa[5], &femur[5], &tibia[5], -10, 40);
        coxa[1] += deltaCoxa;
        coxa[3] -= deltaCoxa;
        coxa[5] -= deltaCoxa;

        delay(timePerStep / 2);
        servoControl(femur[0], tibia[0], coxa[0], femur[1], tibia[1], coxa[1], femur[2], tibia[2], coxa[2],
                     femur[3], tibia[3], coxa[3], femur[4], tibia[4], coxa[4], femur[5], tibia[5], coxa[5]);

        //move them all down
           InverseKinematics(&coxa[0], &femur[0], &tibia[0], 30, 30);
        InverseKinematics(&coxa[2], &femur[2], &tibia[2], 10, 30);
        InverseKinematics(&coxa[4], &femur[4], &tibia[4], 20, 40);
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
